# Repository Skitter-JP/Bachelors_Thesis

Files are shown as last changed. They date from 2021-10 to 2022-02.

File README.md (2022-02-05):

# Bachelors Thesis

CVUT Logo

Topic: Sensorless Field Oriented Control of a Brushless DC Motor

This thesis was written at the Czech Technical University in the department of Circuit Theory.

The Goals of this thesis were

- Select a suitable combination of a microcontroller and power electronics.
- Design the controlling electronics and a printed circuit board.
- Design and implement the controlling algorithm for the estimation of the rotor angle and the field oriented control.

In this repositary the following has been attached

- **Code:** The Code was written in Microchip Studio using C. The USB library has not been included since its not my property.
- **Schematics:** The Schematics and PCBs were designed in Altium. All footprints, symbols and 3D models were manually inserted into my own component library.
- **Boards views:** The 3D views should be opened in Adobe. Github/Chrome does not support 3D PDF models
- **3D Models:** The Motor Mounts, Magnetic Sensor Mounts and Magnet Mounts can be found here.
- **Images:** The manufactured PCB and Mounts can be viewd here.
- **Document:** The thesis document which was submitted

## ESC PCB Board Views

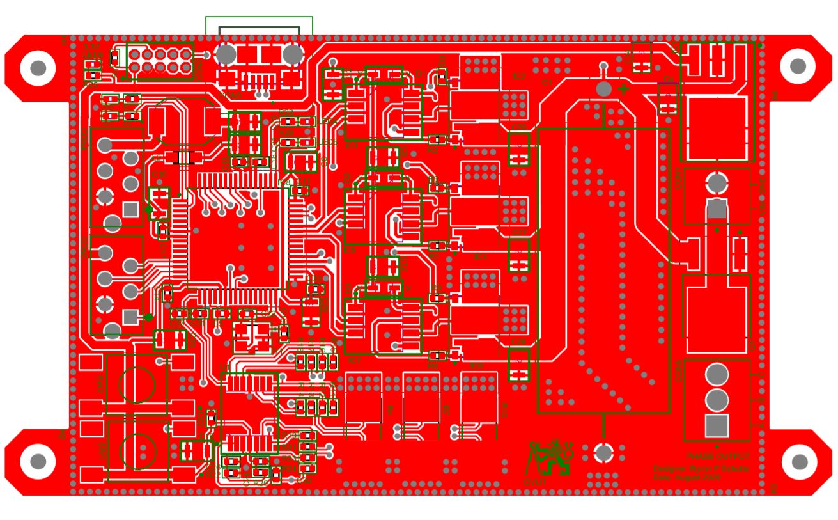
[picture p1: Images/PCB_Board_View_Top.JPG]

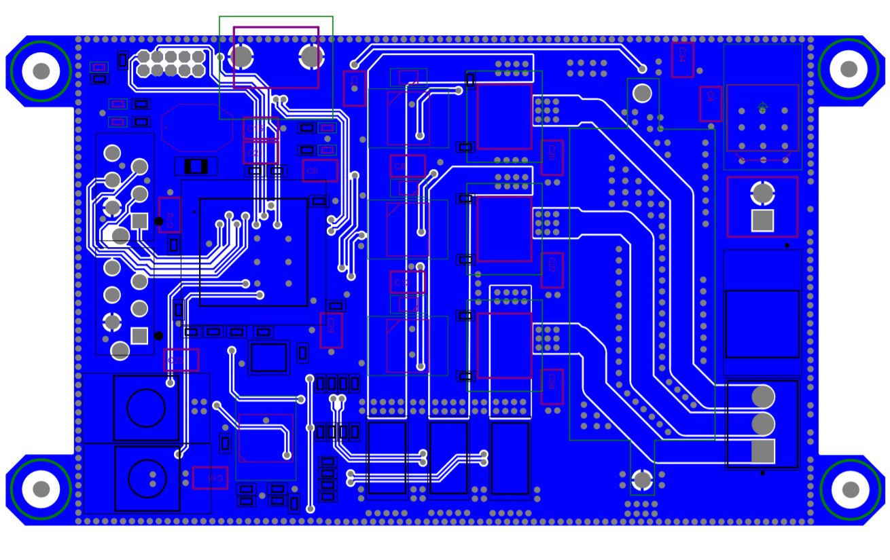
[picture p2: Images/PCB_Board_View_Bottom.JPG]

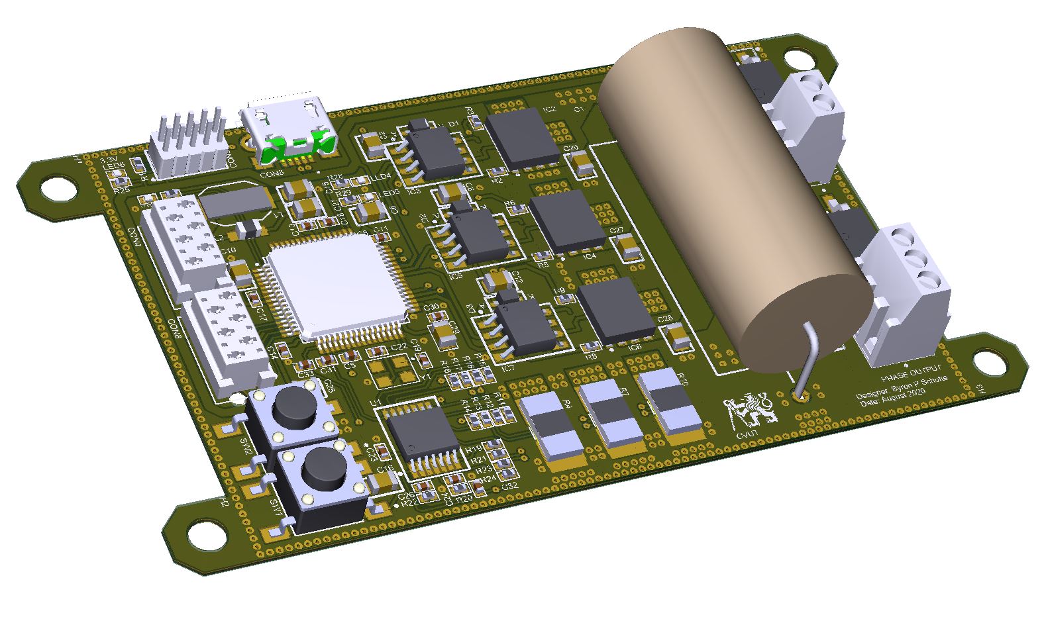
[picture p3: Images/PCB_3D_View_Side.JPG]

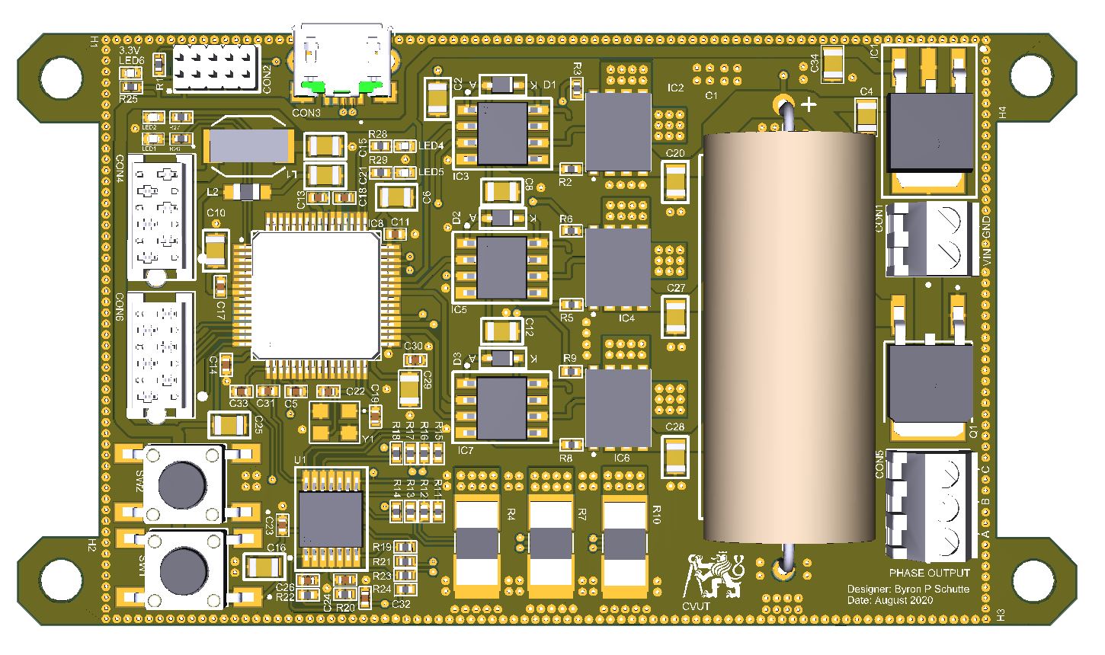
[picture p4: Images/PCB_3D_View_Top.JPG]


## Completed ESC PCB

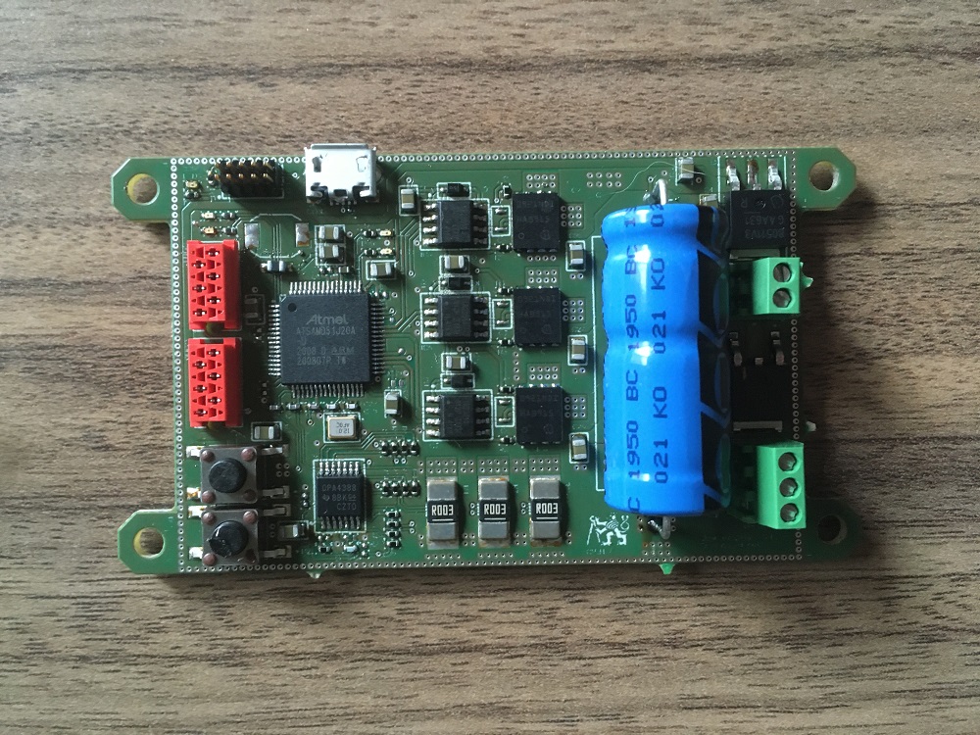
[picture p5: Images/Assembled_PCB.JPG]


## Magnetic Encoder Board Views

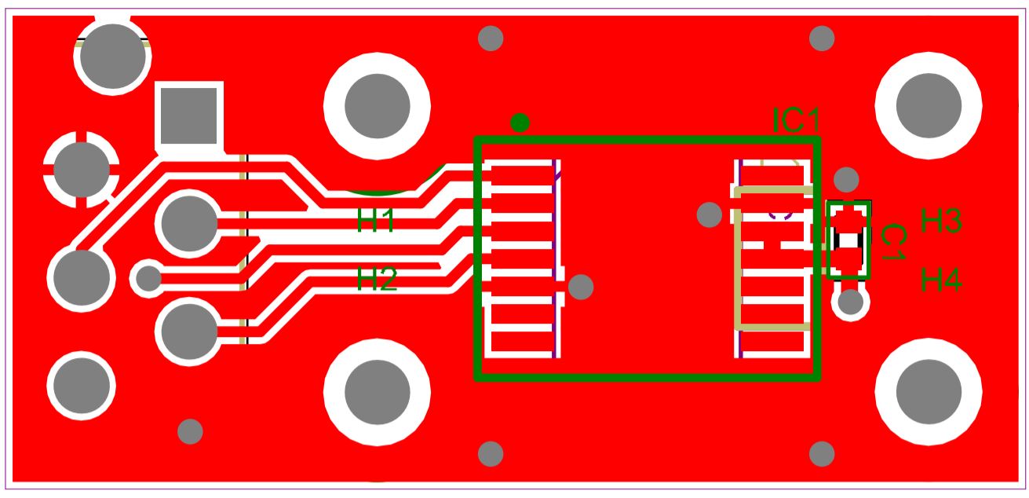
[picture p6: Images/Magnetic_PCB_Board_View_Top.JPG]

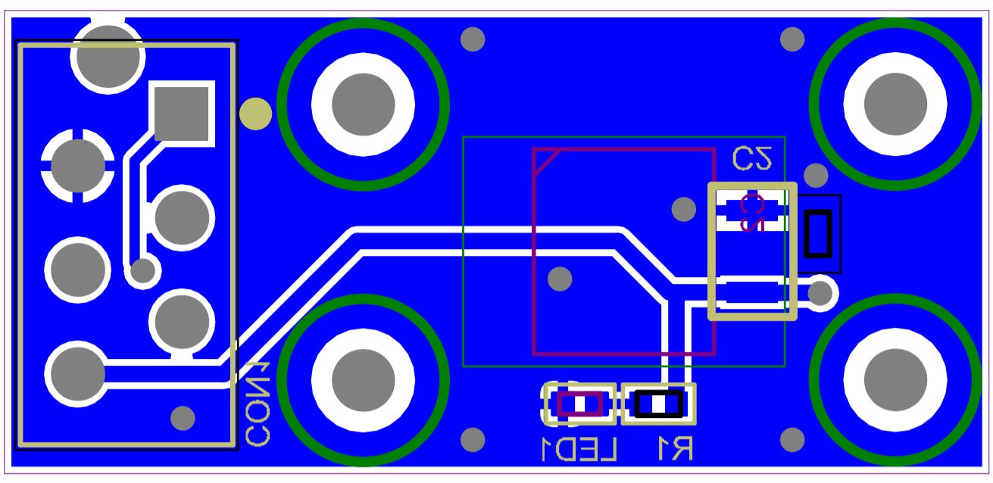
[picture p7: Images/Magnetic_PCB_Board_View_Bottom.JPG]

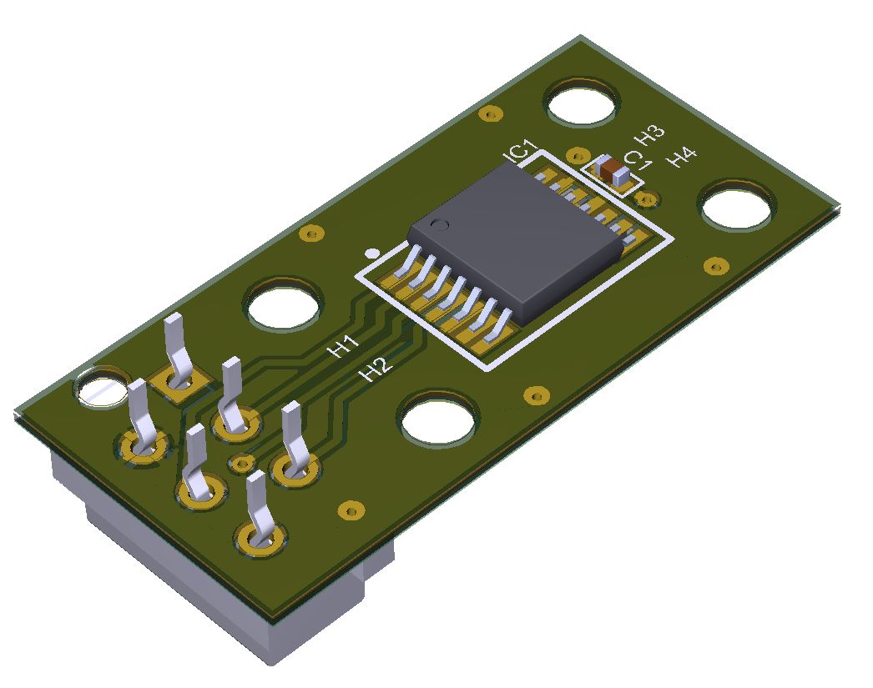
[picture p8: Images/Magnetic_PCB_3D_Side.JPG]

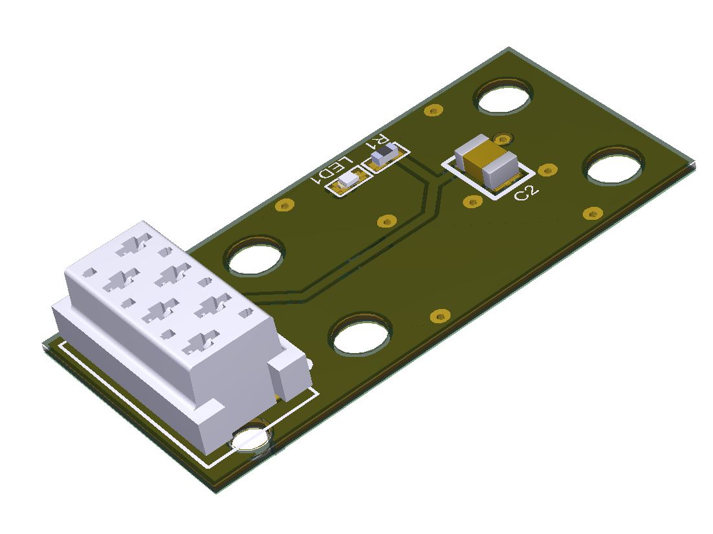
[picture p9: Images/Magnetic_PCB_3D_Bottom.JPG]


## Completed Magnetic Encoder PCB

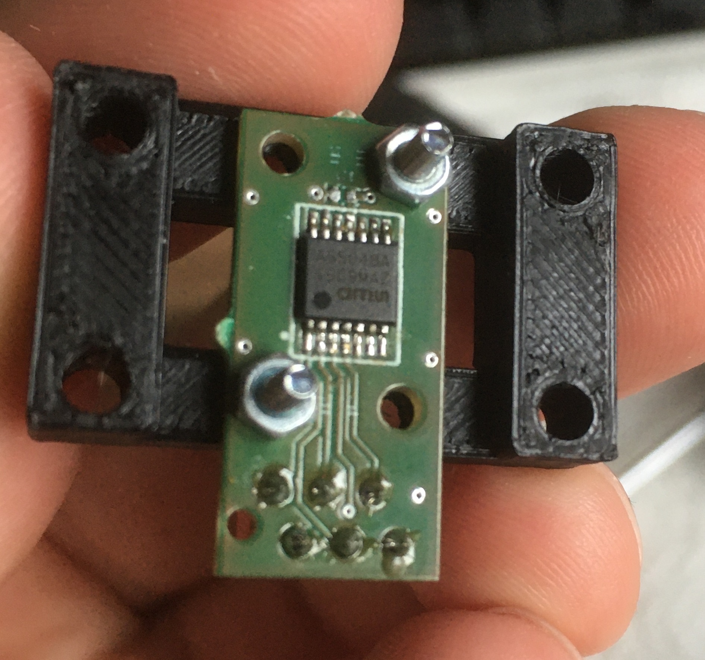
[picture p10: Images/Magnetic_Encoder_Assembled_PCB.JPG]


## Hardware Block Diagram

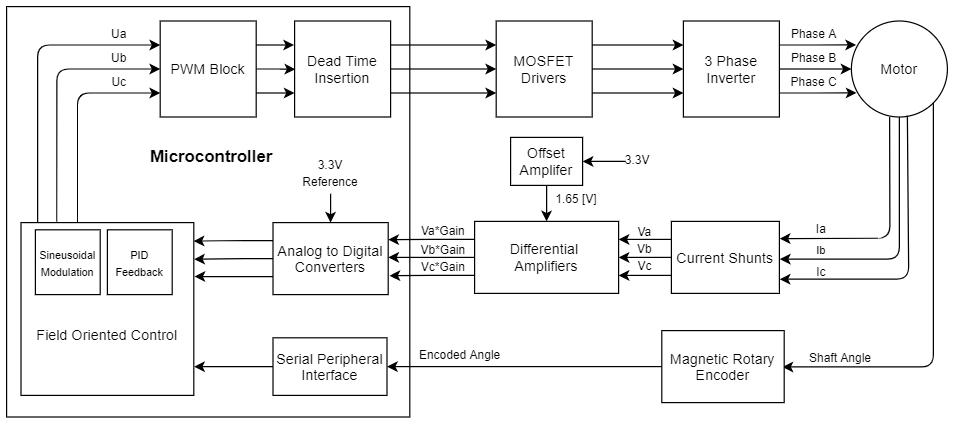
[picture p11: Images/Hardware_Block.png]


## State Observer Block Diagram

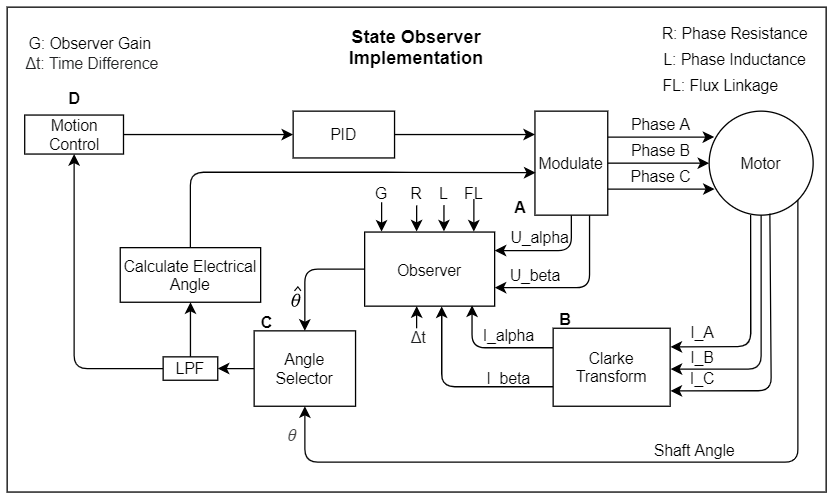
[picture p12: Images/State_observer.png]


- **A:** The modulated voltages 𝑈𝛼 and 𝑈𝛽 are passed into the Observer
- **B:** The currents generated from 𝑈𝛼 and 𝑈𝛽 are read and converted into the same reference frame (𝐼𝛼 and 𝐼𝛽) and then fed into the observer
- **C:** The angle from the observer and the encoder are passed into the angle selector, depending on the sensing mode either angle will be passed in the control loop
- **D:** The control loop handles the given angle and performs the necessary task

## Constant Velocity Mode

The following figure was captured from the ESC while operating in a constant velocity. In the figure the
velocity was set to 5 [rad/sec]. The measured velocity was fluctuating between 20 and -10 rad/sec. The
mean value was centered near 5 rad/sec.

A professor in my defense mentioned that these large fluctuations in the measured velocity were most likely caused from the BLDC motor.
A BLDC motor is designed for trapezoidal wave forms, if a BLAC motor would of been used these large fluctuations in the measured velocity would of not been apparent.

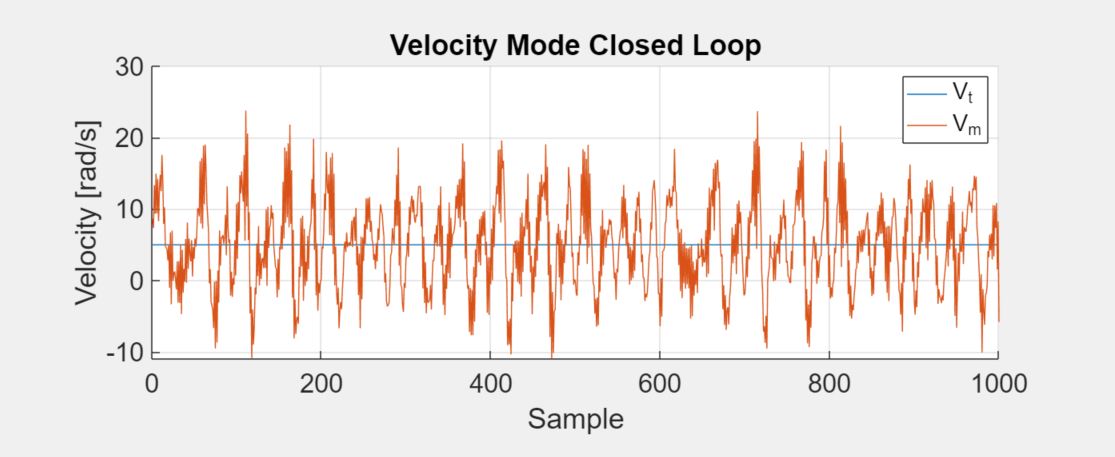
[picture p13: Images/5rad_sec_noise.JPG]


- **Vt:** Target Velocity
- **Vm:** Measured Velocity

## Current Sensing Results

The following figures were captured from the ESC while operating in a constant velocity mode at 5
rad/sec. In the first figure the motor was running with no mechanical load, the wave form appears noisy, but a sinusoidal signal is visible.
In the second figure a mechanical load was placed on the motor, this increased the consumed current. The wave form is clear with minimal noise.

Current capture **with no** mechancal load on the motor

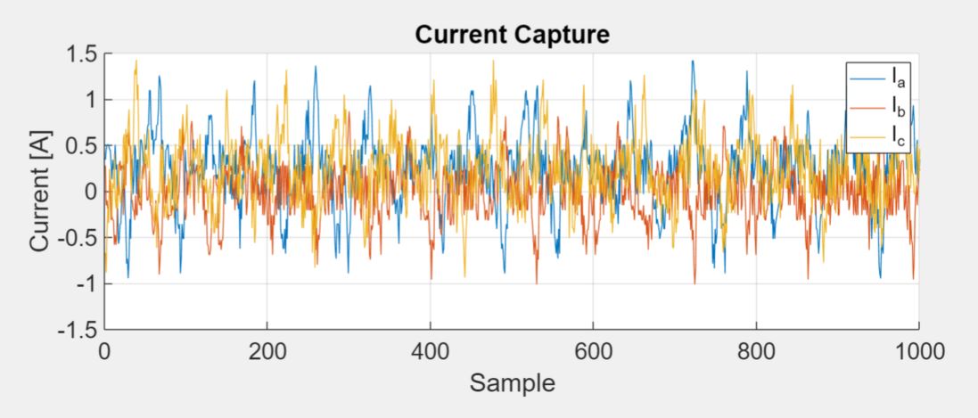
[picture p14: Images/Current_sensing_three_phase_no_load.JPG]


Current capture **with** a mechancal load on the motor

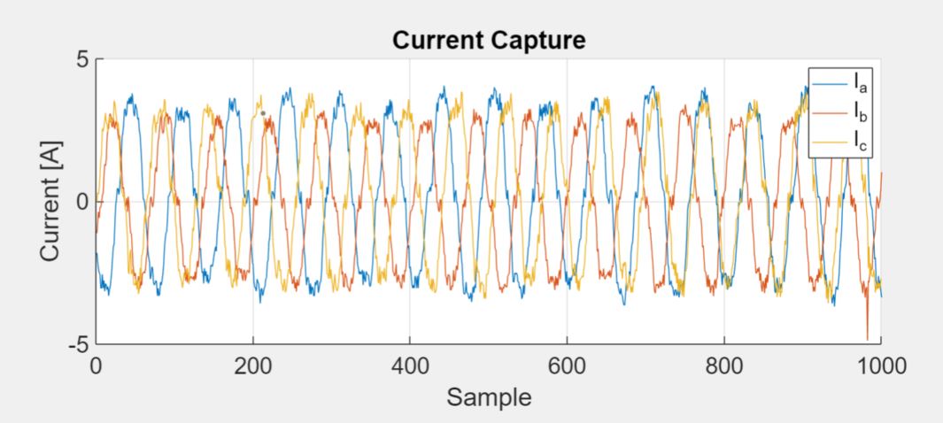
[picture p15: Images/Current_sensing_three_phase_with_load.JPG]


## Maintain Set Angle Results

The following figures demonstrate the angle closed loop functionality. In the figure below the set angle is 5 rad.
The motor shaft was mechanically displaced in both directions, the shaft returned its set point with slight over and undershoots.

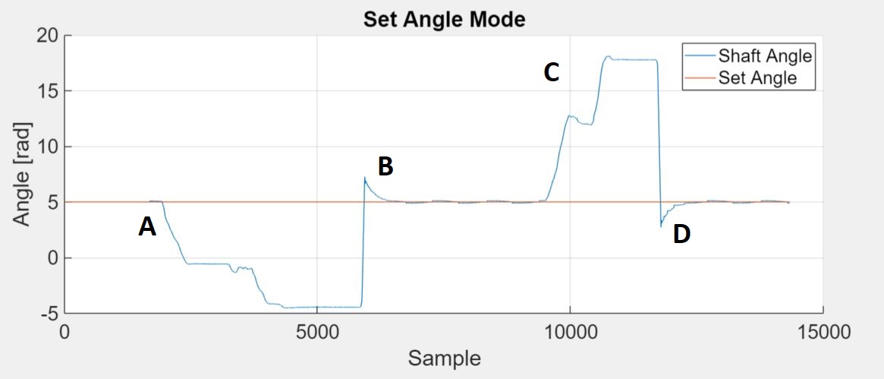
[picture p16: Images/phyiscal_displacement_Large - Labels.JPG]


- **A:** The shaft is displaced 5 rad in a negative direction
- **B:** The shaft is released, an overshoot occurs
- **C:** The shaft is displaced 15 rad in the positive direction
- **D:** The shaft is released, an undershoot occurs

## Angle Estimation Results

A state observer was implemented to estimate the angle of the motor shaft using
voltages/currents in the rotating reference frame. Estimating the shaft of the angle was possible but
was not stable. The state observer would saturate due to noise in the current measurements, therefor
to keep the estimated angle stable a load needed to be applied to the motor to push the currents out
of the noise floor.

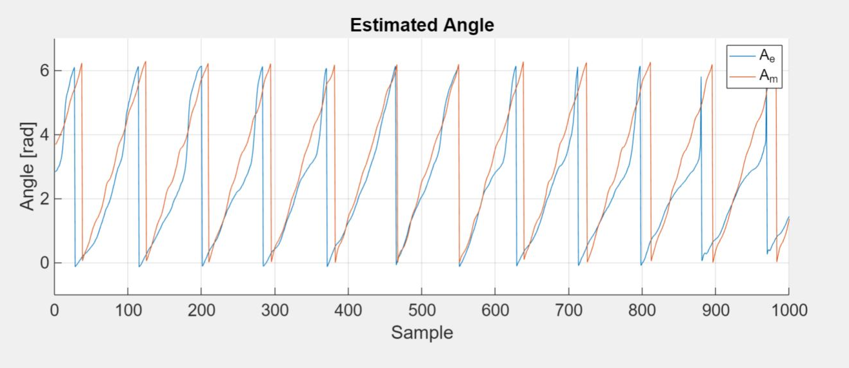
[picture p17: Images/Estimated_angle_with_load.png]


- **Ae:** Estimated Angle
- **Am:** Measured Angle 

## 3D Printed Mounts

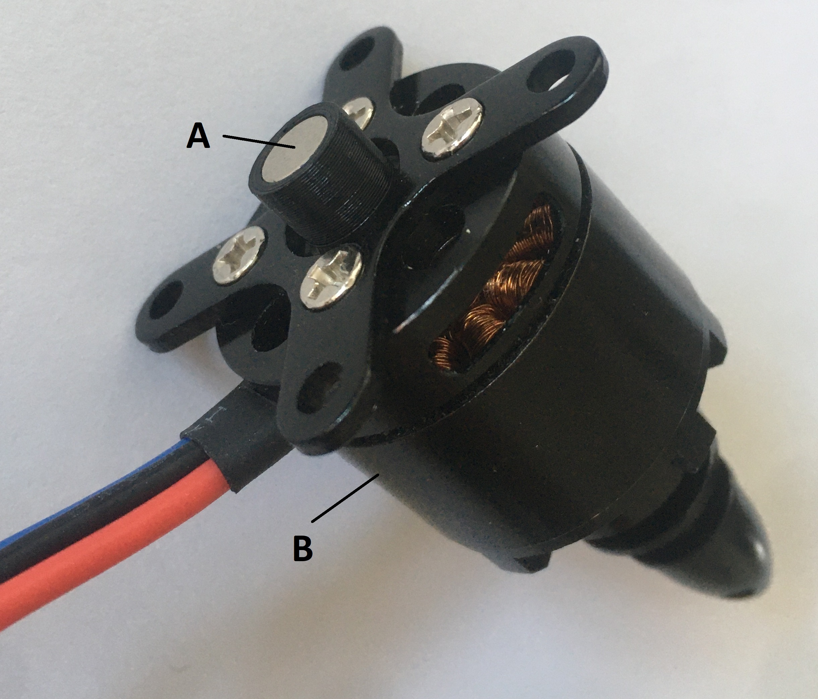
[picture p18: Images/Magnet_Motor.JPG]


- **A:** A small mount for a diametrically magnetized magnet which was mounted to the rotor.
- **B:** A BLDC Motor

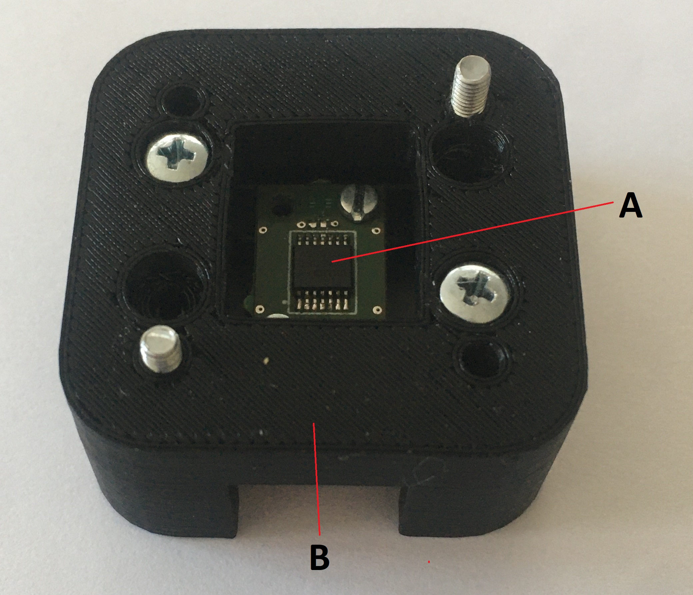
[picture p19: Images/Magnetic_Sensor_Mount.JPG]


- **A:** The magnetic encoder which was mounted just below the rotor.
- **B:** A 3D printed Motor/Magnetic encoder Mount

## Notes
1. I wanted to split the code up into seperate libraries but this obvisouly did not happen, so please excuse the mess.
2. My supervisor encouraged me to tightly layout the PCB and use small footprints. The smallest being 0402 packages, this was also a challange to solder but worth the effort.
3. The graphs and data seen in the document were created in MATLAB
4. The motor and magnetic mount were created in SketchUp 3D

Lastly, credit must be given to the [ArduinoFOC](https://github.com/simplefoc/Arduino-FOC) project. I spent weeks reading their code and porting ideas over to my project.

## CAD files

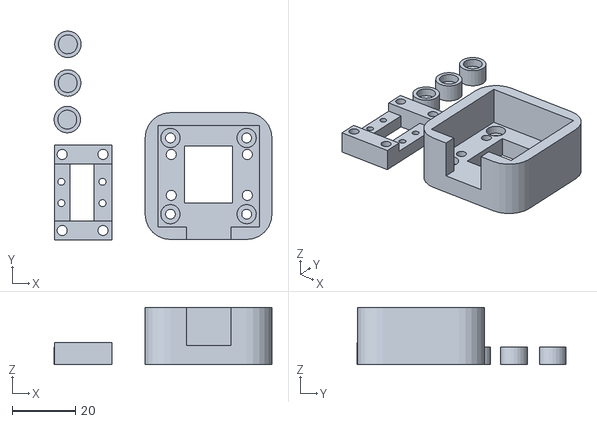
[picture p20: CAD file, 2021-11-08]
3D Models/Prints_fixed.stl
68.8 x 65.9 x 18.0

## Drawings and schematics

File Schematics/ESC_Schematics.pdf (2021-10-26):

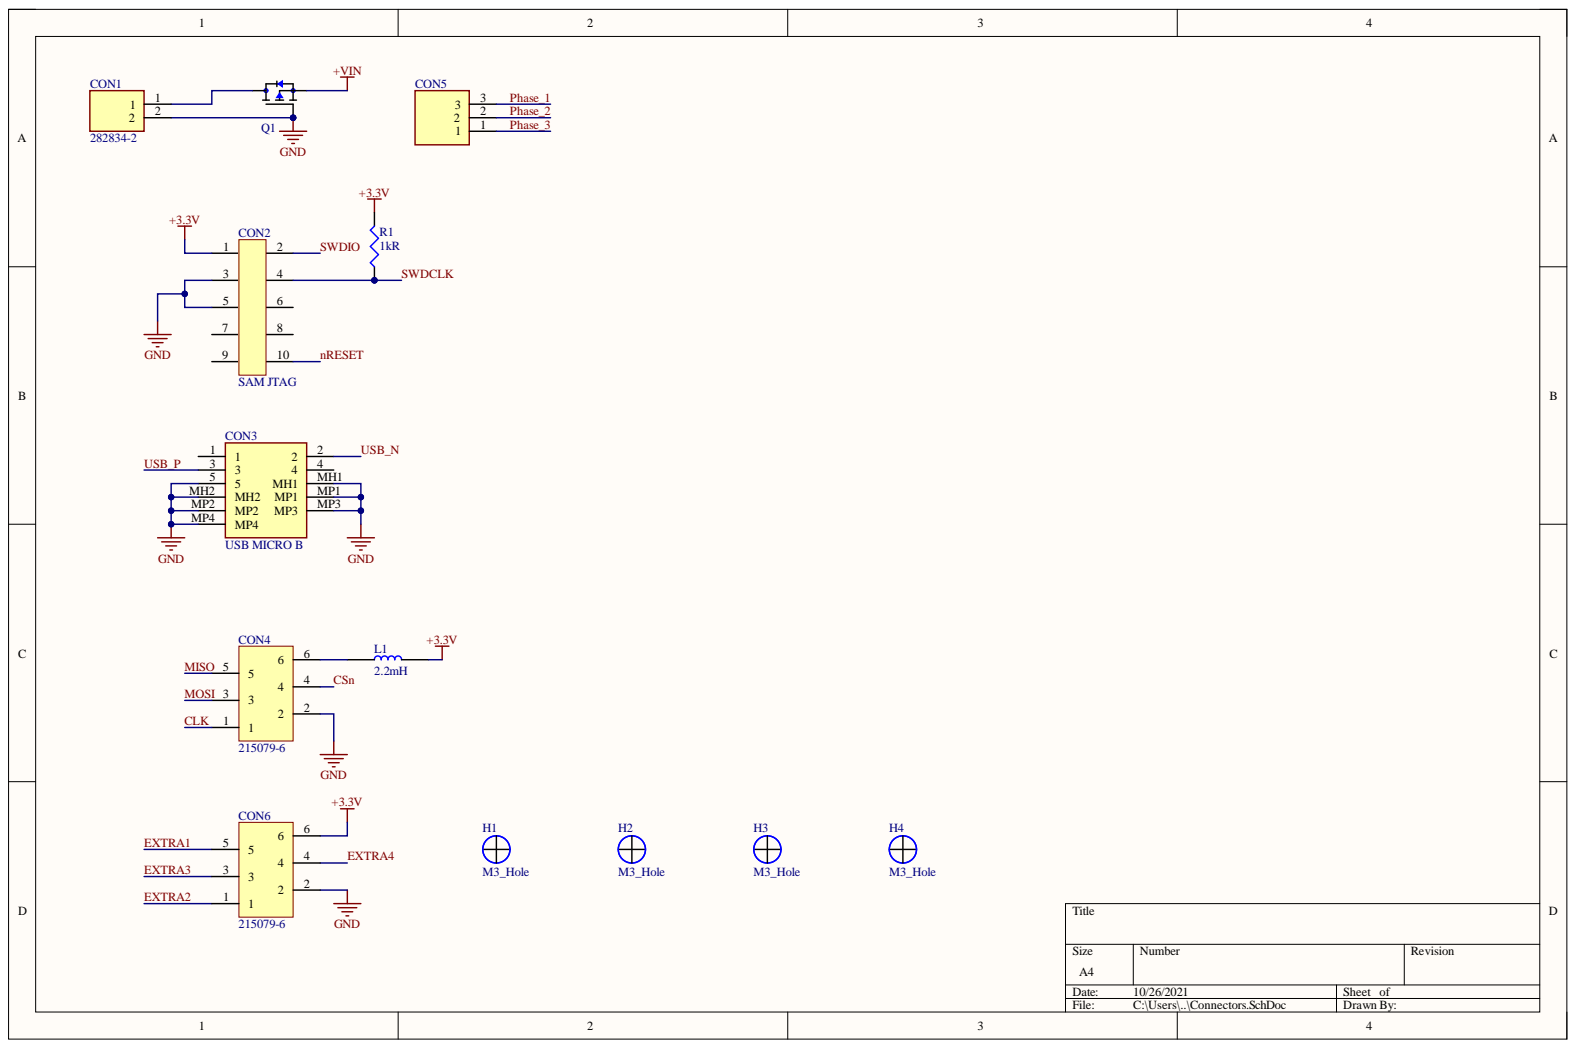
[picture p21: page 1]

Size A4 | Number | Revision

Date: 10/26/2021 | Sheet of
File: C:\Users\..\Connectors.SchDoc | Drawn By:

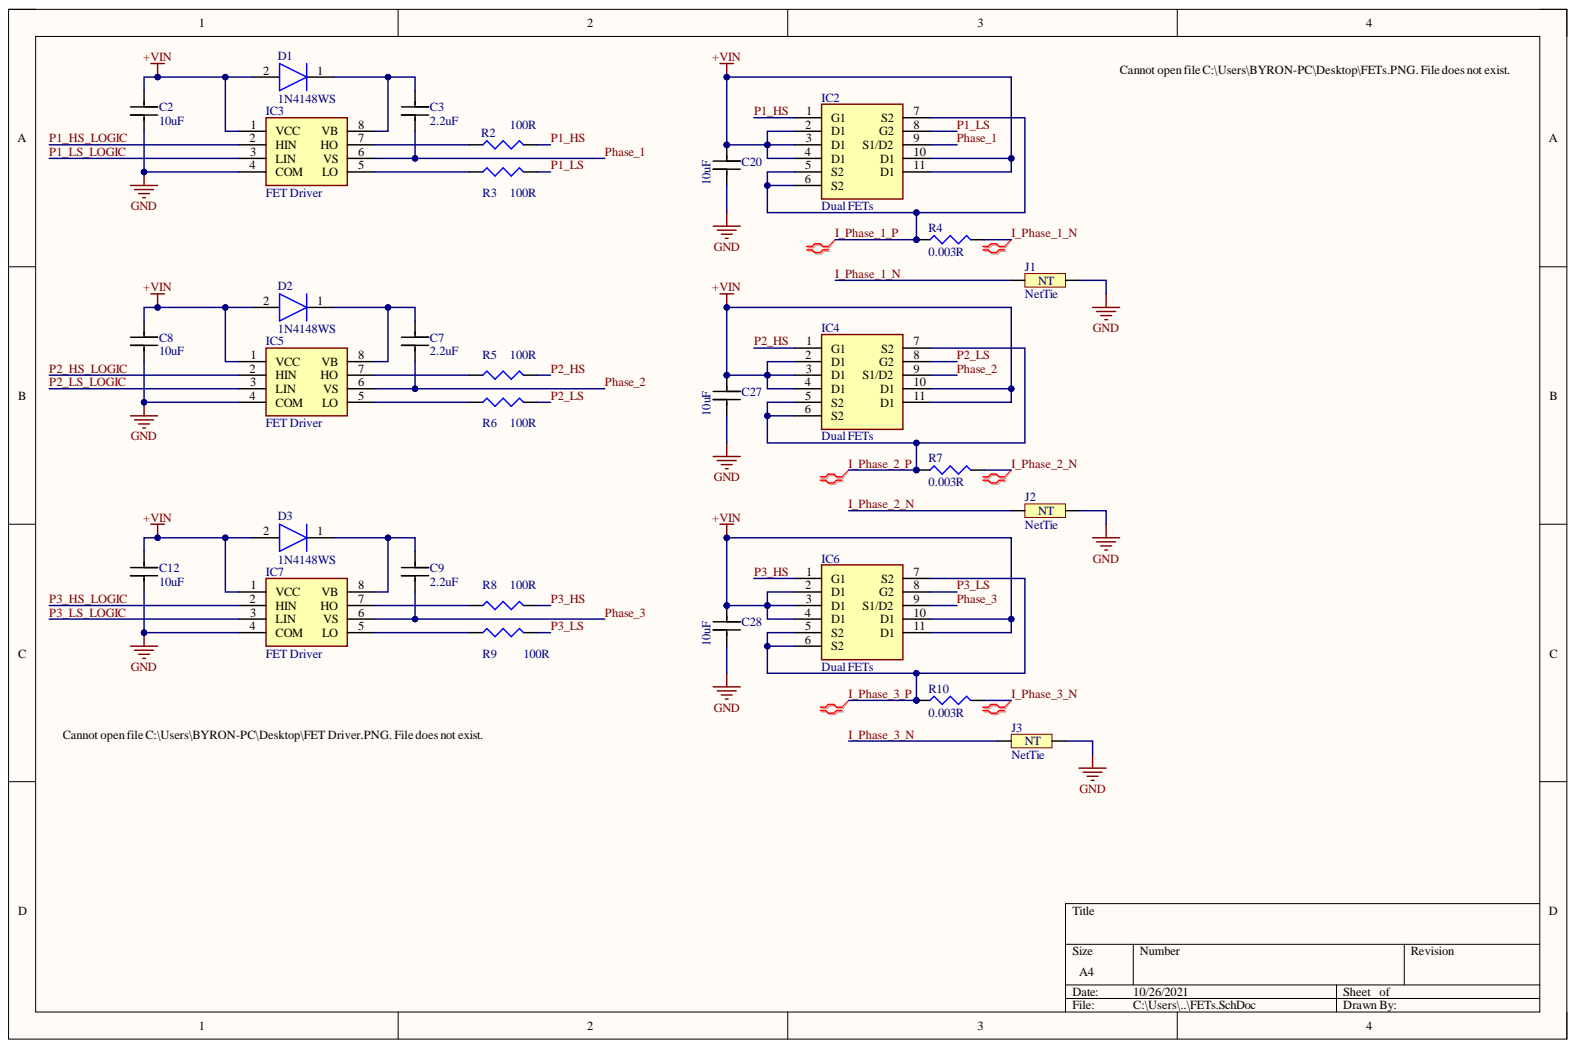
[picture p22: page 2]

Siz e A4 | Numb e r | R evisio n

Da te : 10/26/20 2 1 | She et of
File : C:\Use rs\. .\FETs. S c hD o c | Dr awn B y :

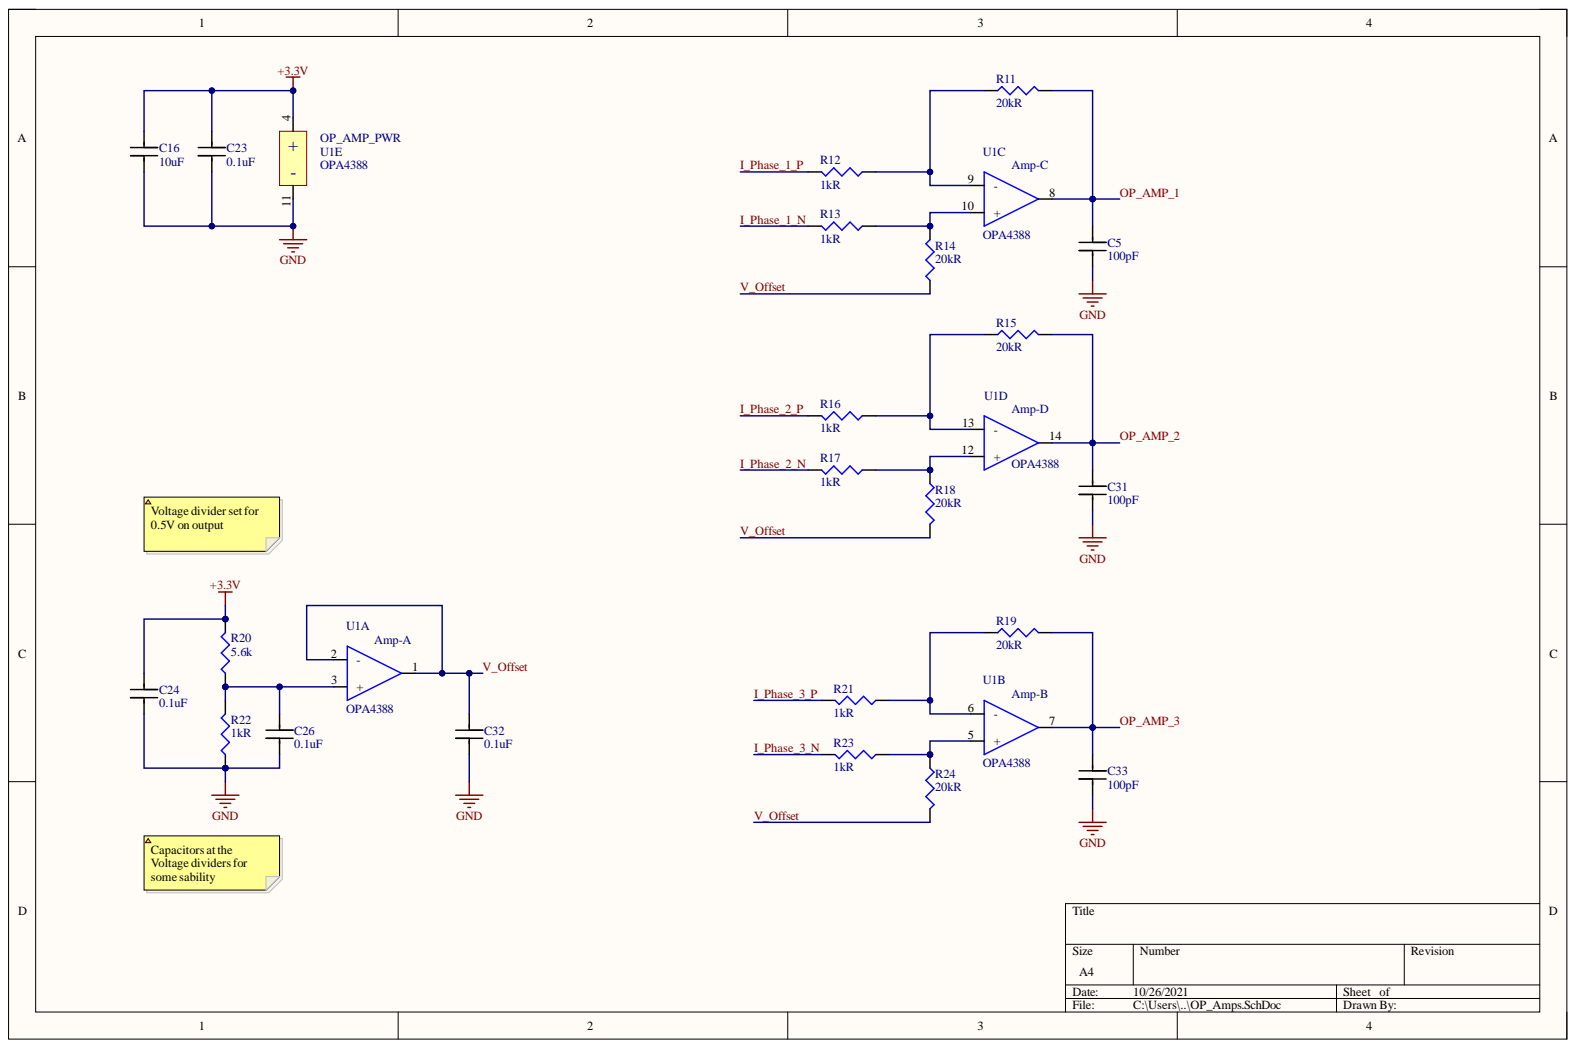
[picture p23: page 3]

some sability Voltage divide
0.5V on output

Siz e A4 | Numb e r | R evisio n

Da te : 10/26/20 2 1 | She et of
File : C:\Use rs\. .\OP_Amp s . S c hD o c | Dr awn B y :

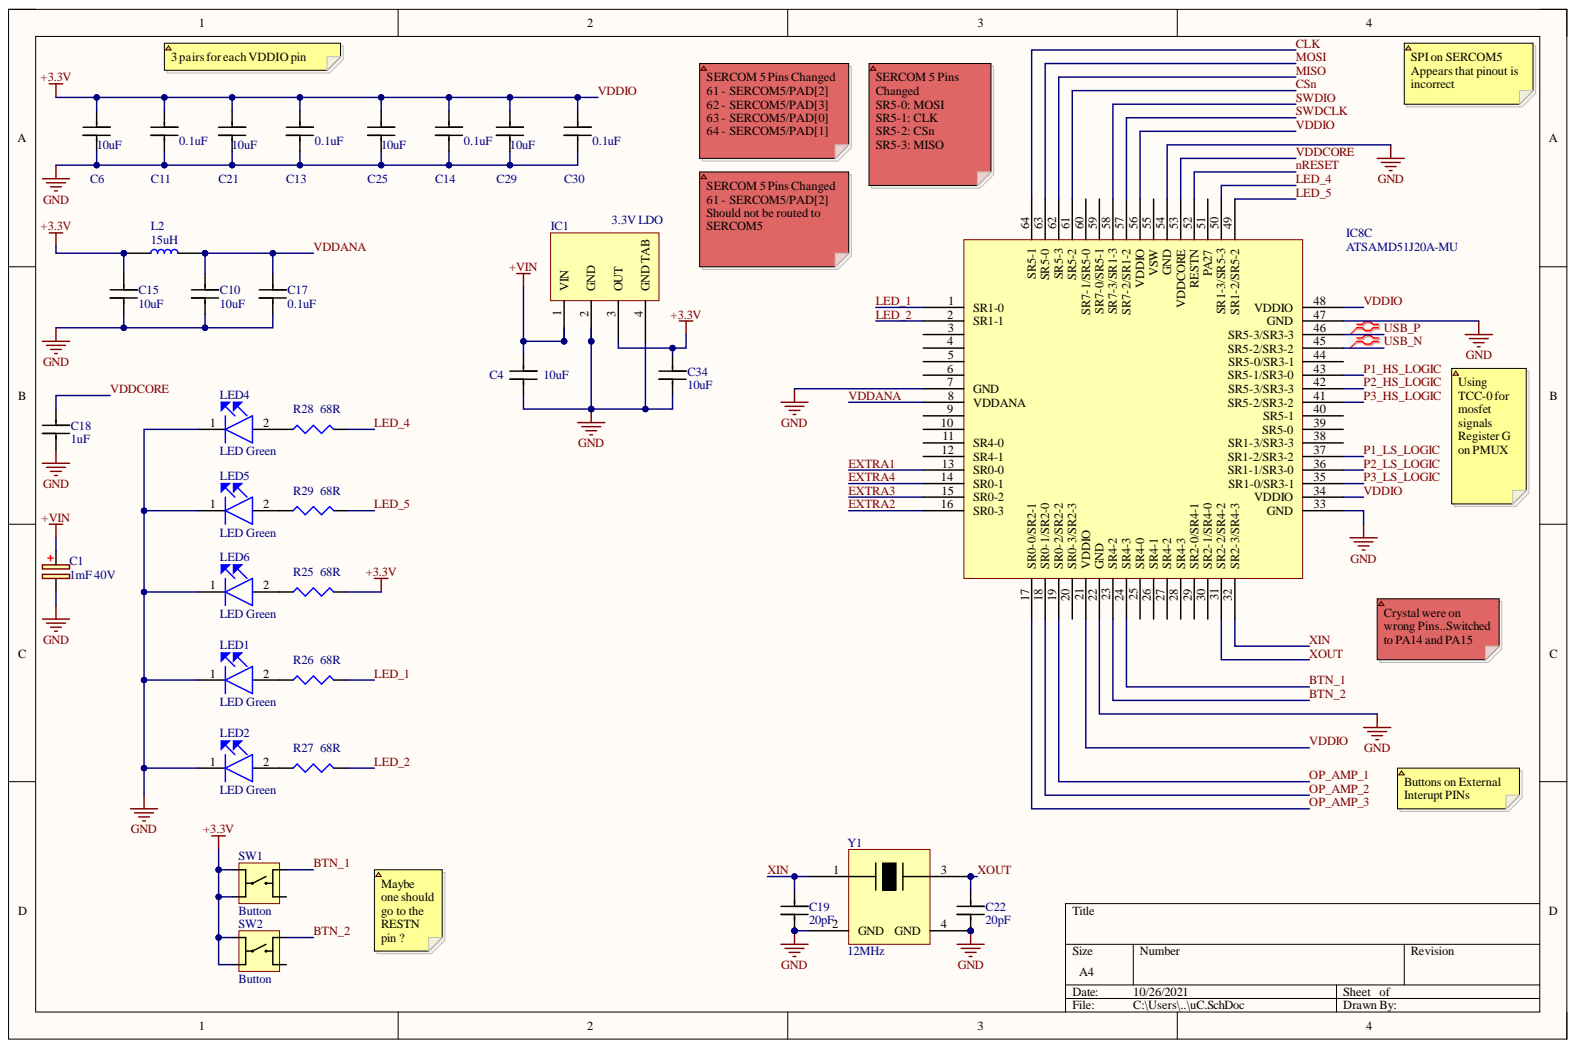
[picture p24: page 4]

CLK

VDDC O RE nRES ET LED _4 LED _5

SR1-2/SR5-2 49 SR1-3/SR5-3 50 PA27 51 RESTN 52 VDDCORE 53 GND 54 VSW 55 VDDIO 56 SR7-2/SR1-2 57 SR7-3/SR1-3 58 SR7-0/SR5-1 59 SR7-1/SR5-0 60 SR5-2 61 SR5-3 62 SR5-0 63 SR5-1 64

one should
go to the RESTN

Siz e A4 | Numb e r | R evisio n

Da te : 10/26/20 2 1 | She et of
File : C:\Use rs\. .\uC . S c hD o c | Dr awn B y :

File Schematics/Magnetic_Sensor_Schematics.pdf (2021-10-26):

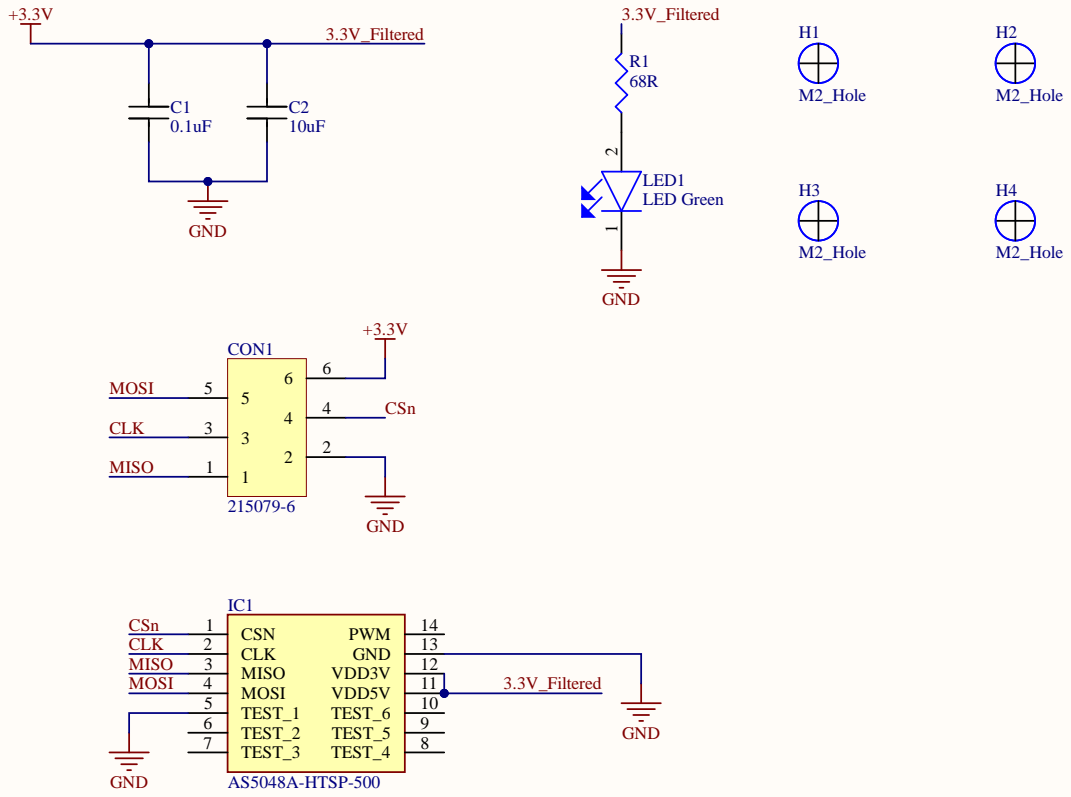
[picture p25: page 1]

MOSI 4 | 3.3V_Filtered
TEST_1 5

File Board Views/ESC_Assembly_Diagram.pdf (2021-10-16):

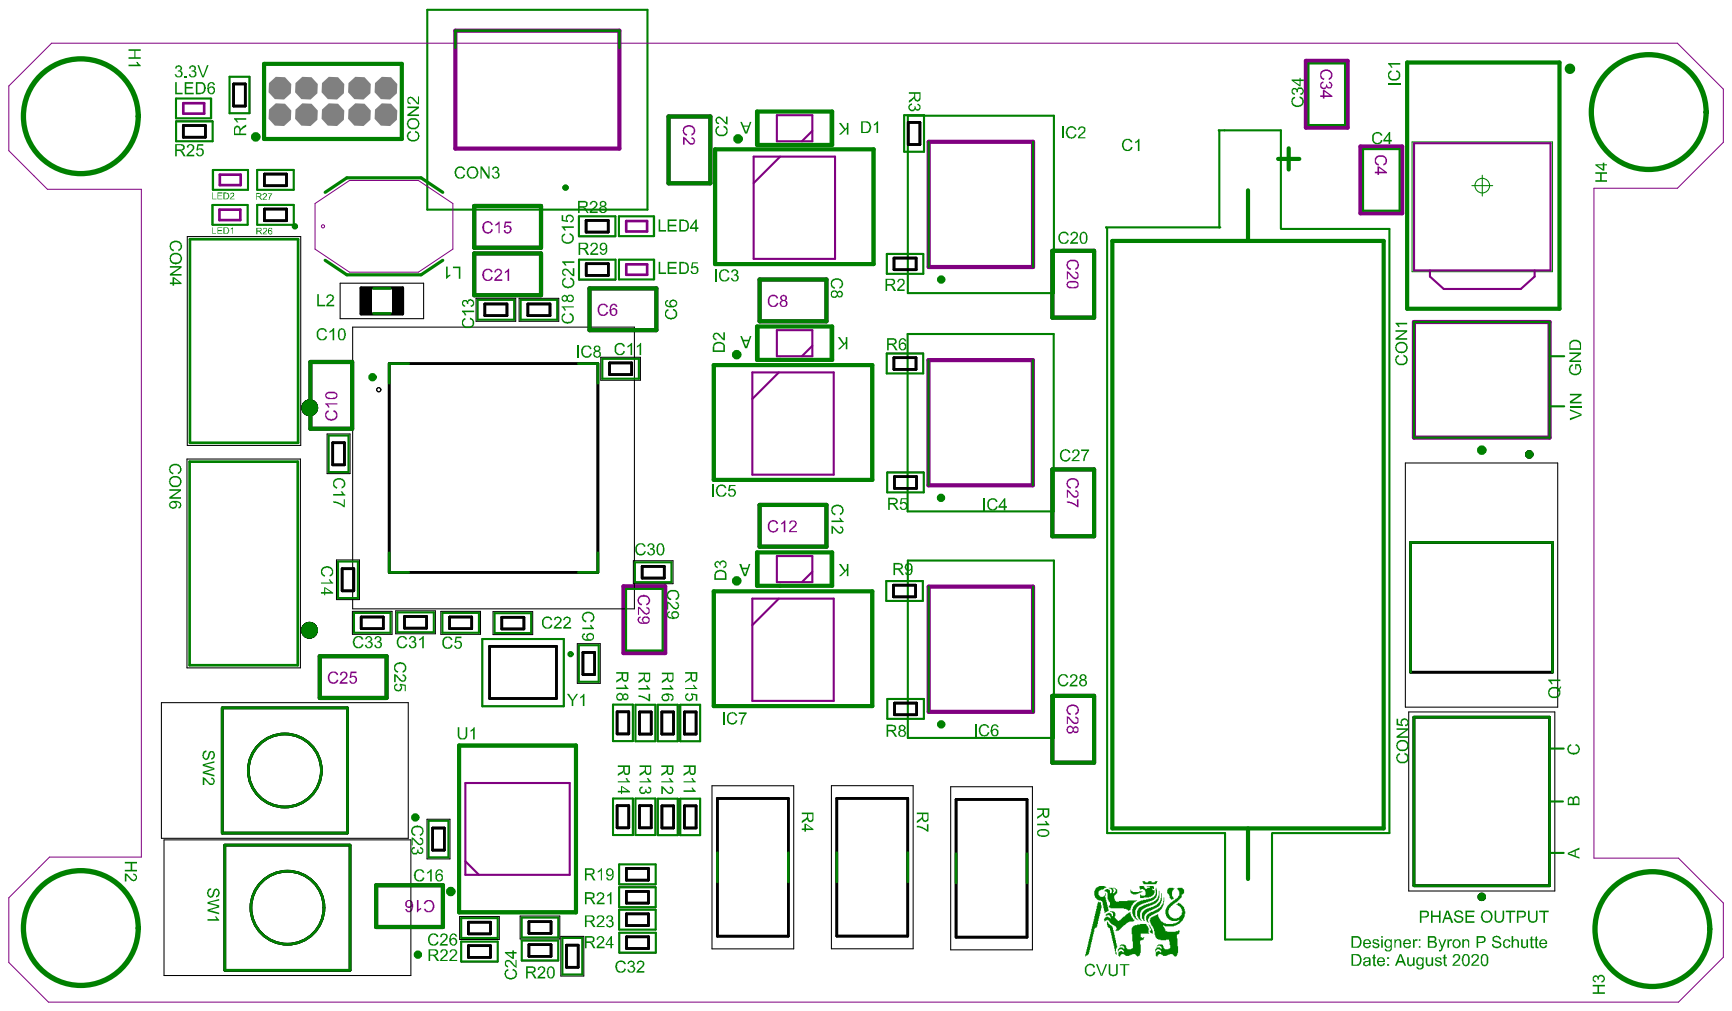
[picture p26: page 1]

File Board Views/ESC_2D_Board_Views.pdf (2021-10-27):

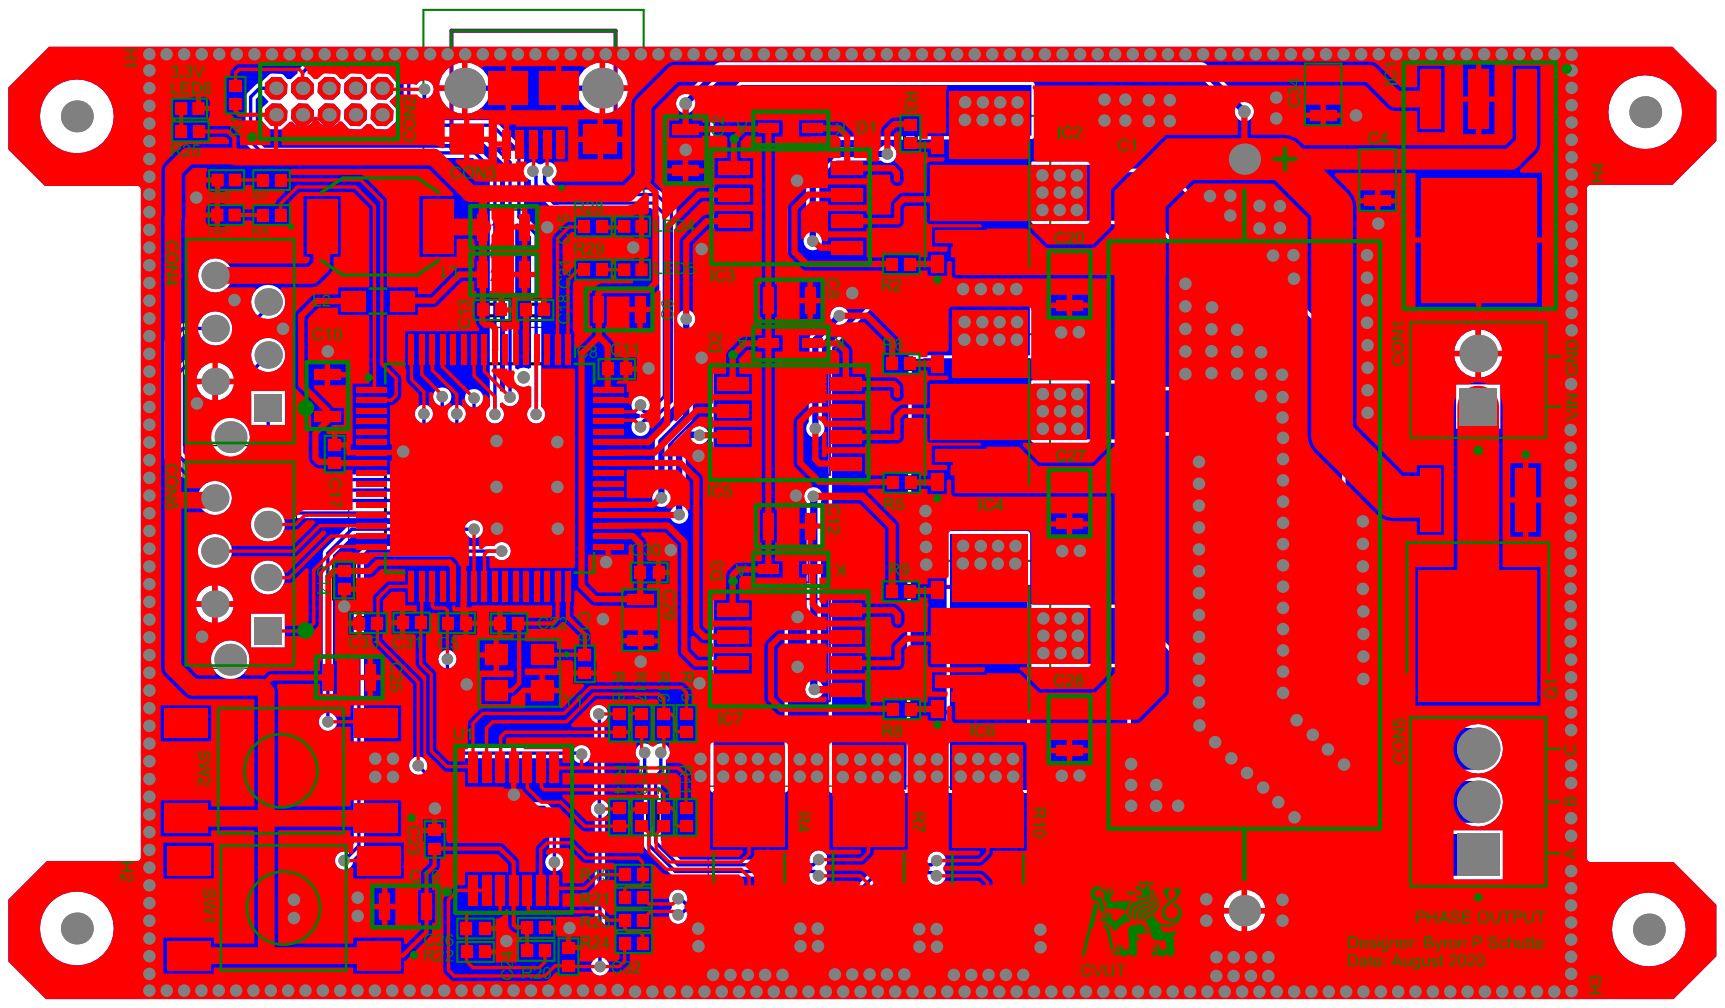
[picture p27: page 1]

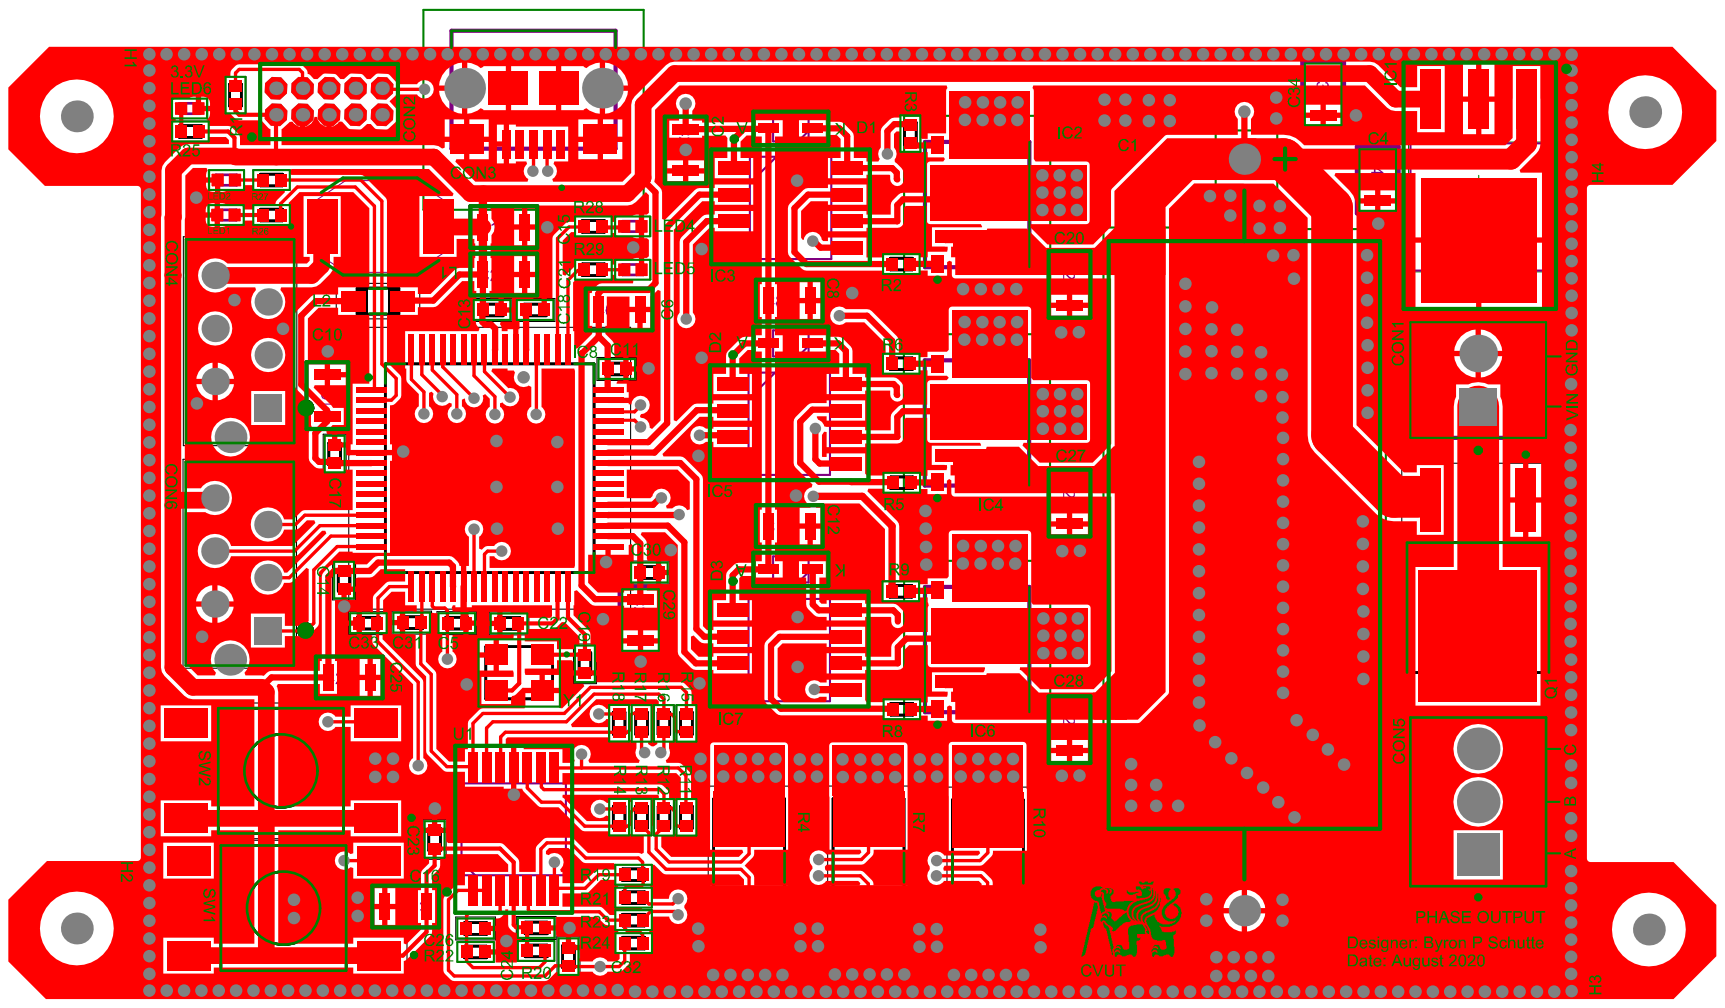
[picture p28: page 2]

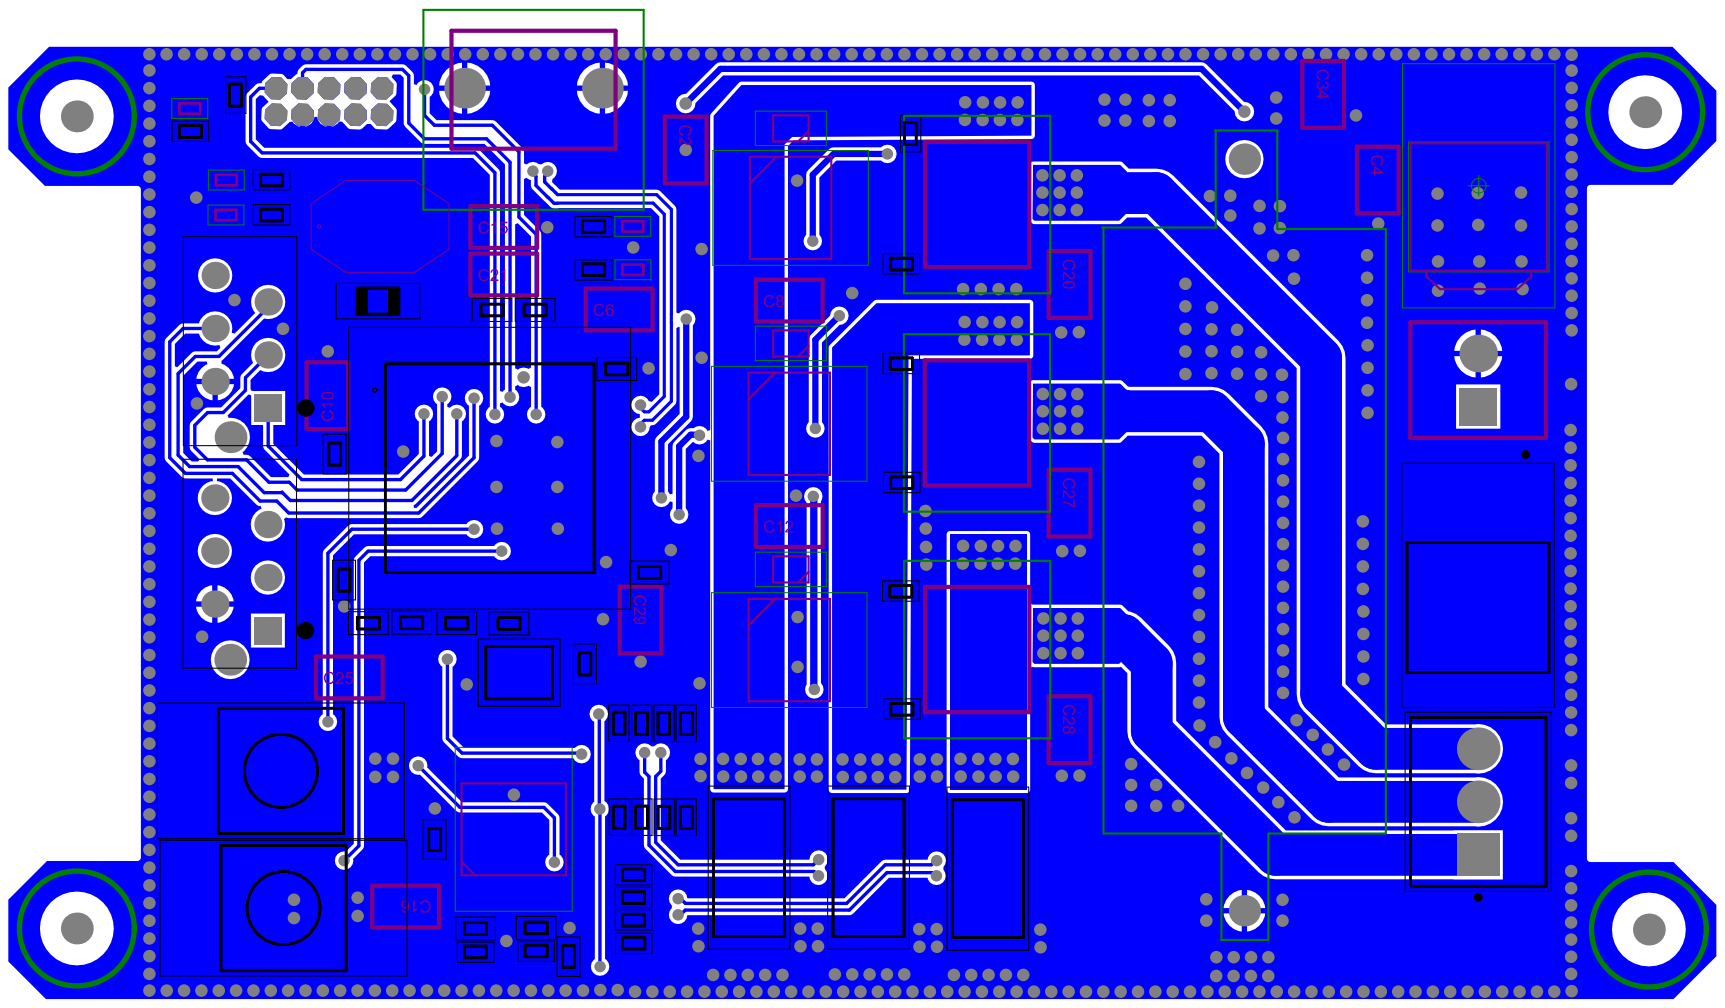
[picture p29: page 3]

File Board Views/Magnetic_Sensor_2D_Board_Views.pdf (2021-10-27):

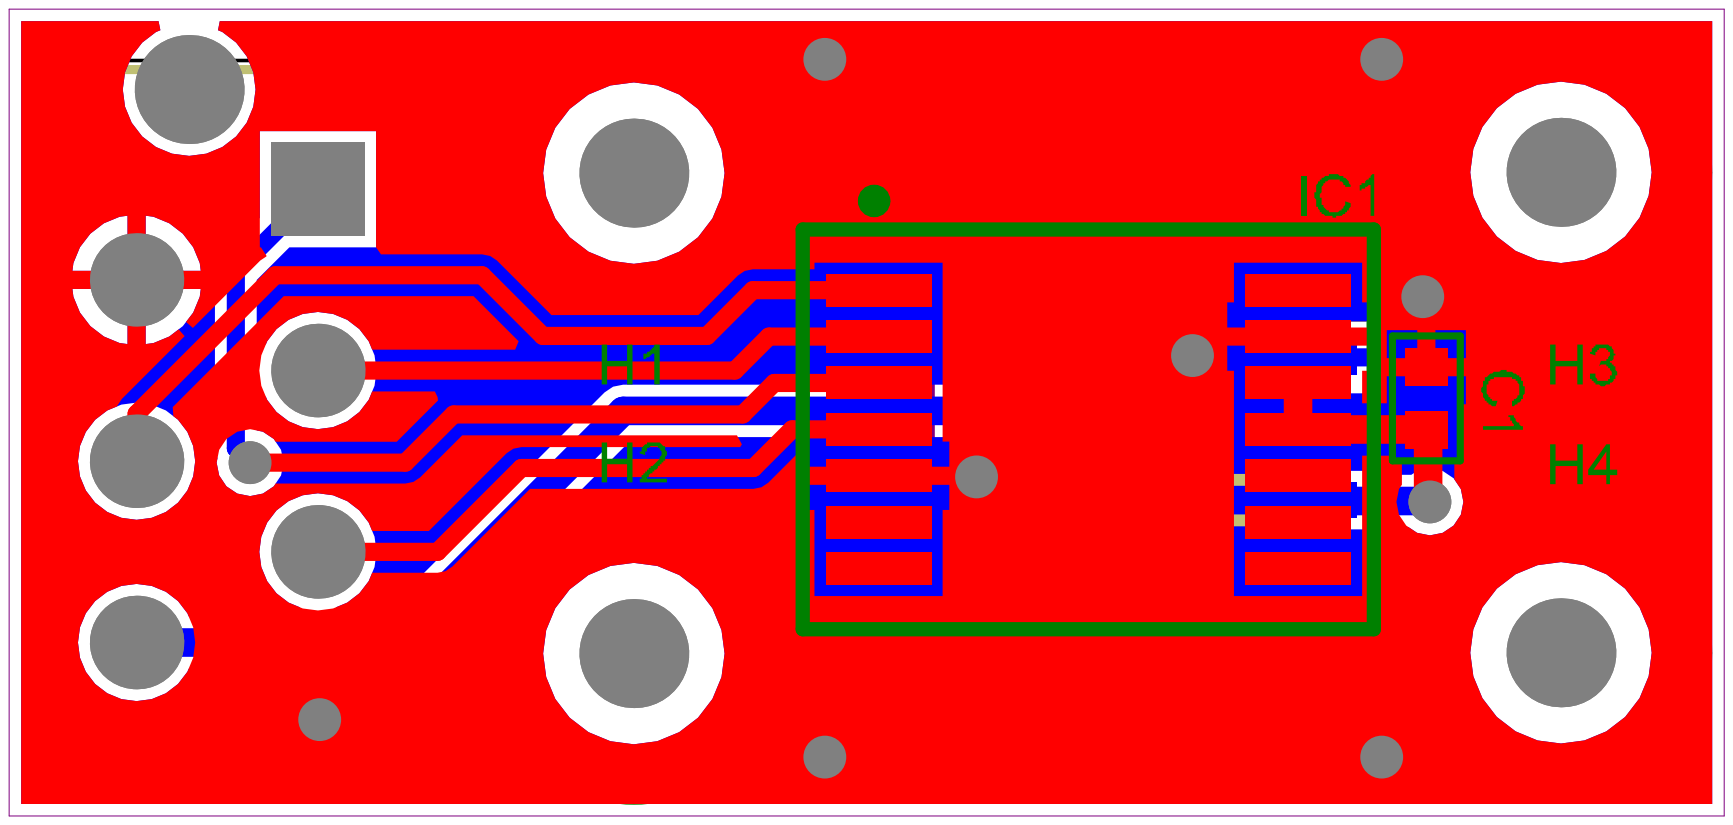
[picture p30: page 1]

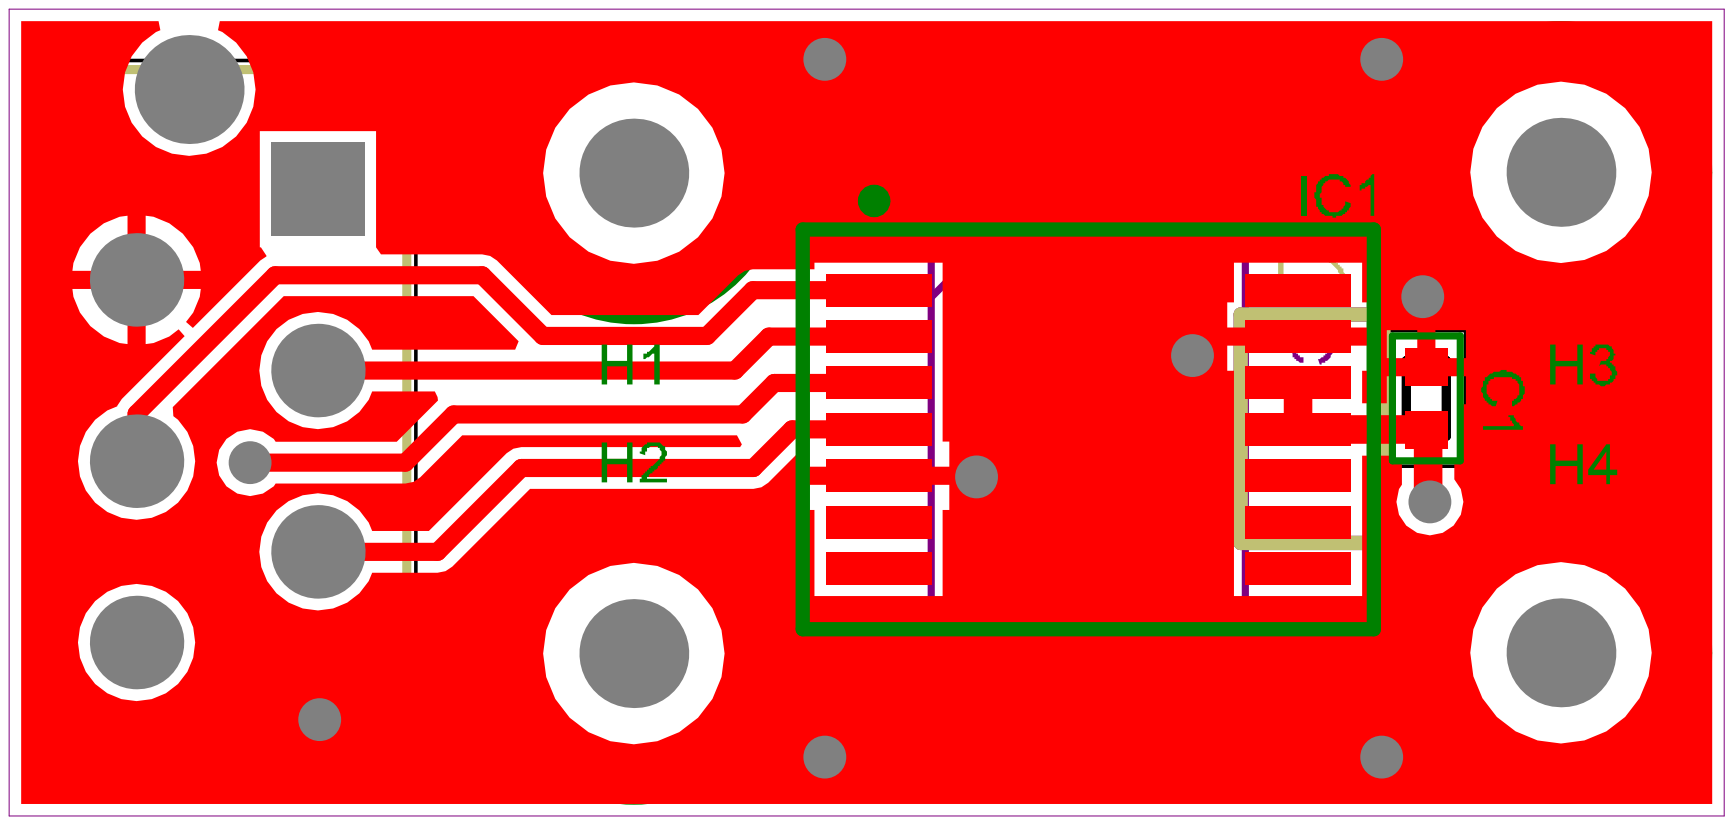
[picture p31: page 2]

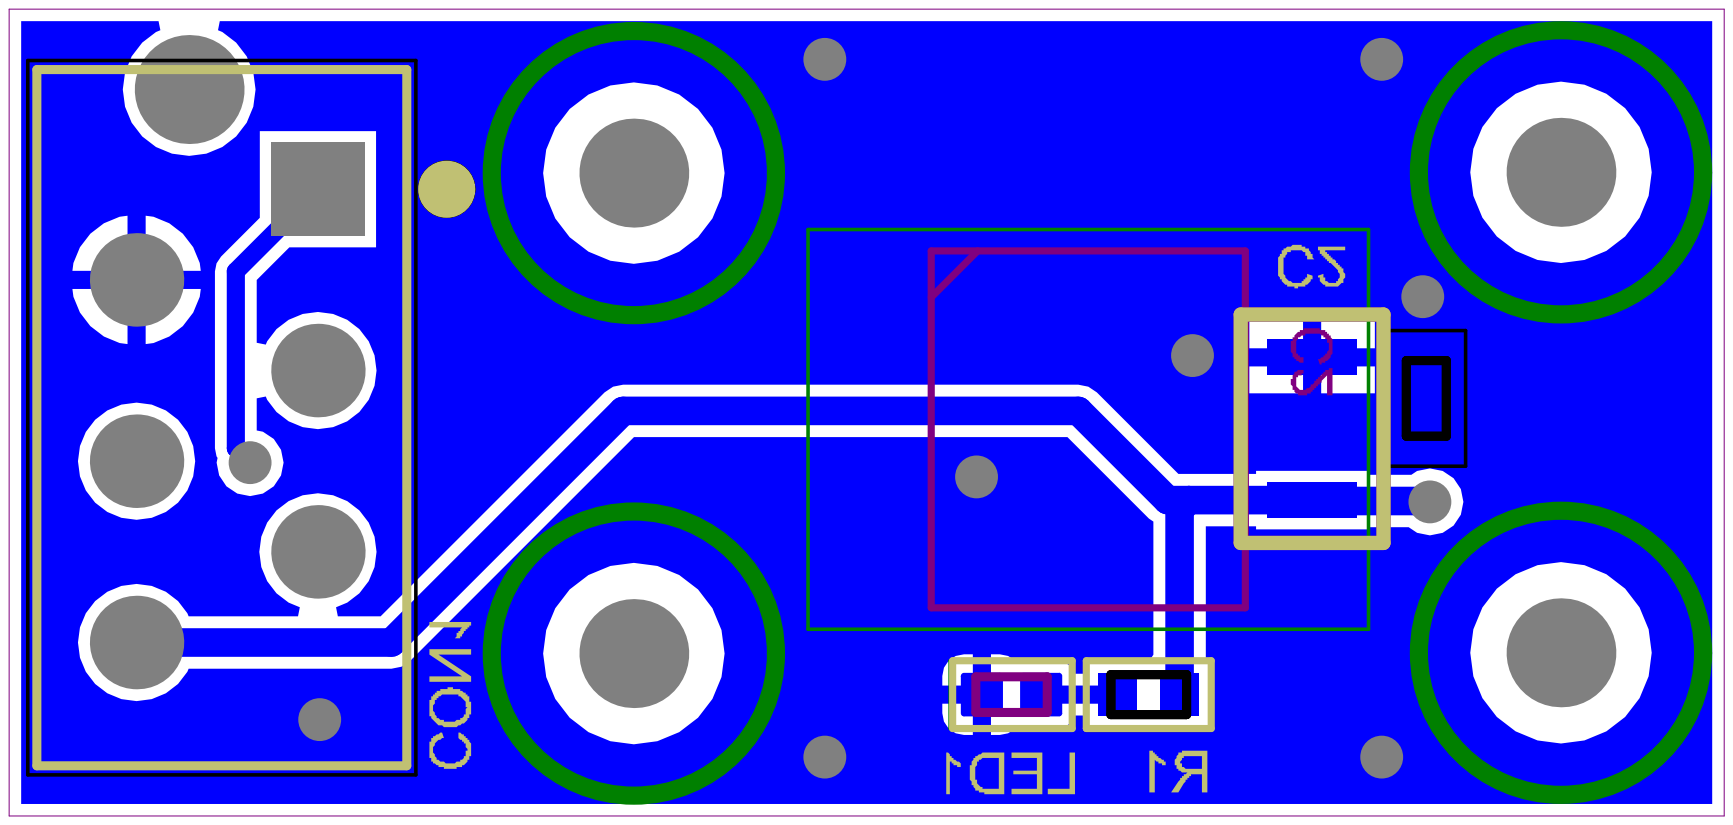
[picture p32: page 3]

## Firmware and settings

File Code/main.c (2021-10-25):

#include "sam.h"
#include "pin_macros.h"
#include "pinout.h"
#include "USB.h"
#include <string.h>
#include <math.h>
#include "tgmath.h"

typedef struct PID_struct{
	
	float P; //!< Proportional gain
	float _I; //!< Integral gain
	float D; //!< Derivative gain
	float output_ramp; //!< Maximum speed of change of the output value
	float limit; //!< Maximum output value
	float integral_prev; //!< last integral component value
	float error_prev; //!< last tracking error value
	unsigned long timestamp_prev; //!< Last execution timestamp
	float output_prev;  //!< last pid output value
	
}PID_struct;

typedef struct LPF_struct{
	
	volatile float Tf; //!< Low pass filter time constant
	volatile unsigned long timestamp_prev;  //!< Last execution timestamp
	volatile float y_prev; //!< filtered value in previous execution step
	
}LPF_struct;

typedef struct PWM_struct{

	float voltage_power_supply;
	float voltage_limit;

	float PWM_resolution;

	int modulation_type;

	volatile float dc_a;
	volatile float dc_b;
	volatile float dc_c;

}PWM_struct;

typedef struct OBSERVER_struct{

	unsigned long timestamp_prev; 
	unsigned long timestamp_now; 

	float flux_linkage;
	float observer_gain;	
	
	float x2;
	float x1;
	
	float flux_vector_alpha;
	float flux_vector_beta;
	
	volatile float xa;
	
	volatile float xb;

}OBSERVER_struct;

typedef struct MOTOR_struct{
	
	_Bool sensorless;

	int pole_pairs;
	int motor_state;

	float phase_resistance;
	float inductance;
	float flux_linkage;
	float observer_gain;

	float current_limit;

	float current_sp;
	
	volatile float exact_shaft_angle;
	
	volatile float shaft_angle;
	
	volatile float shaft_velocity;

	volatile float estimated_angle;
	
	volatile float measured_angle;

	volatile float electrical_angle;

	
	volatile float U_phase_A;
	volatile float U_phase_B;
	volatile float U_phase_C;
	
	volatile float U_q;
	volatile float U_d;
	
	volatile float U_q_prime;
	volatile float U_d_prime;
	
	volatile float U_alpha;
	volatile float U_beta;
	
	volatile float U_alpha_prime;
	volatile float U_beta_prime;
	
	volatile float I_phase_A;
	volatile float I_phase_B;
	volatile float I_phase_C;
	
	volatile float I_q;
	volatile float I_d;
	
	volatile float I_alpha;
	volatile float I_beta;
	
	
	
}MOTOR_struct;

typedef struct CURRENT_SENSE_struct{
	
	

	float shunt_resistor;
	float reference_voltage;
	float gain;
	float bit_rate;

	float volts_to_amps_ratio;

	float I_phase_A_offset;
	float I_phase_B_offset;
	float I_phase_C_offset;

	float I_gain_phase_A;
	float I_gain_phase_B;
	float I_gain_phase_C;

	float conversion_scalar;
	
	volatile uint32_t I_raw_phase_A;
	volatile uint32_t I_raw_phase_B;
	volatile uint32_t I_raw_phase_C;
	
	volatile float I_raw_phase_A_voltage;
	volatile float I_raw_phase_B_voltage;
	volatile float I_raw_phase_C_voltage;
	
	volatile _Bool read_currents;


}CURRENT_SENSE_struct;

enum Sensor_Direction{
	CLOCK_WISE = 1,
	COUNTER_CLOCK_WISE = -1,
	NONE
};

enum modulation{
	SINE_PWM,
	SPVM
};

enum calcuations{
	APROXIMATE,
	COMPUTE
};

enum states{
	DISABLED = 0,
	ENABLED = 1,
	UNKNOWN = 2
};

enum phases{

	PHASE_A = 1,
	PHASE_B = 2,
	PHASE_C = 3
	
};

enum bools{
	FALSE = 0,
	TRUE = 1
};

enum motions{
	ANGLE = 0,
	ANGLE_OPENLOOP = 1,
	VELOCITY = 2,
	VELOCITY_OPENLOOP = 3,
	TORQUE = 4
};

#define _NOP() do { __asm__ __volatile__ ("nop"); } while (0)

#define bitRead(value, bit) (((value) >> (bit)) & 0x01)
#define bitSet(value, bit) ((value) |= (1UL << (bit)))
#define bitClear(value, bit) ((value) &= ~(1UL << (bit)))
#define bitWrite(value, bit, bitvalue) (bitvalue ? bitSet(value, bit) : bitClear(value, bit))
#define bit(b) (1UL << (b))


//#define CPU_CLK (120000000ul) 
#define F_CPU	(120000000ul) //120 MHz

#define SERCOM_SPI_FREQ_REF 48000000 // 48MHz

//NaN and Infinity checks
#define UTILS_IS_INF(x)		((x) == (1.0 / 0.0) || (x) == (-1.0 / 0.0))
#define UTILS_IS_NAN(x)		((x) != (x))
#define UTILS_NAN_ZERO(x)	(x = UTILS_IS_NAN(x) ? 0.0 : x)

// Value for PCHCTRLm Mapping
#define GCLK_TCC0 25
#define GCLK_TCC2 29
#define GCLK_TC0 9

#define PORT_MUX_B 1
#define PORT_MUX_D 3
#define PORT_MUX_F 5
#define PORT_MUX_G 6
#define PORT_MUX_H 7

//For Clock Setup
#define GENERIC_CLOCK_GENERATOR_MAIN      (0u)
#define GENERIC_CLOCK_GENERATOR_XOSC32K   (3u)
#define GENERIC_CLOCK_GENERATOR_48M		  (1u)
#define GENERIC_CLOCK_GENERATOR_48M_SYNC	GCLK_SYNCBUSY_GENCTRL1
#define GENERIC_CLOCK_GENERATOR_100M	  (2u)
#define GENERIC_CLOCK_GENERATOR_100M_SYNC	GCLK_SYNCBUSY_GENCTRL2
#define GENERIC_CLOCK_GENERATOR_12M       (4u)
#define GENERIC_CLOCK_GENERATOR_12M_SYNC   GCLK_SYNCBUSY_GENCTRL4
#define MAIN_CLOCK_SOURCE				  GCLK_GENCTRL_SRC_DPLL0
#define GENERIC_CLOCK_GENERATOR_1M		  (5u)
//For Clock Setup - END


#define _sign(a) ( ( (a) < 0 )  ?  -1   : ( (a) > 0 ) )
#define _round(x) ((x)>=0?(long)((x)+0.5):(long)((x)-0.5))
#define _constrain(amt,low,high) ((amt)<(low)?(low):((amt)>(high)?(high):(amt)))
#define min(a,b) ((a)<(b)?(a):(b))
#define max(a,b) ((a)>(b)?(a):(b))
#define _sqrt(a) (_sqrtApprox(a))

// utility defines
#define _2_SQRT3 1.15470053838
#define _SQRT3 1.73205080757
#define _1_SQRT3 0.57735026919
#define _SQRT3_2 0.86602540378
#define _SQRT2 1.41421356237
#define _120_D2R 2.09439510239
#define _PI 3.14159265359
#define _PI_2 1.57079632679
#define _PI_3 1.0471975512
#define _2PI 6.28318530718
#define _3PI_2 4.71238898038
#define _PI_6 0.52359877559
#define _2PI_3 2.094395102 //120 deg
#define _4PI_3 4.188790205 //240 deg
#define _SQRT3_2 0.86602540378


#define velocity_limit 20 //[rad/sec]

//This will limit the amount of call to the ADC and observer ?
#define FOC_CONTROL_LOOP_FREQ_DIVIDER	3


//Command for the Magnetic Sensor, can be defined ...
const uint16_t AS5048A_NOP                           = 0x0000; // Dummy operation, no information.
const uint16_t AS5048A_CLEAR_ERROR_FLAG              = 0x0001; // Error register. All errors are cleared by access.
const uint16_t AS5048A_PROGRAMMING_CONTROL           = 0x0003; // Register control programming. Programming must be enabled before the memory is burned. Before programming verification is mandatory. See Programming Procedure.
const uint16_t AS5048A_OTP_REGISTER_ZERO_POS_HIGH    = 0x0016; // Zero value of 8 bits high
const uint16_t AS5048A_OTP_REGISTER_ZERO_POS_LOW     = 0x0017; // Zero value 6 bits lower
const uint16_t AS5048A_DIAG_AGC                      = 0x3FFD; // (0-7) The value of the automatic gain control. 0 decimal represents a high magnetic field, 255 decimal represents a low magnetic field. (8-13) Diagnostics Flags
const uint16_t AS5048A_MAGNITUDE                     = 0x3FFE; // The value of the output power CORDIC
const uint16_t AS5048A_ANGLE                         = 0x3FFF; // Angular output value, including zero position correction Resolution_ADC 14-bit resolution (0.0219 ° / LSB)



static volatile uint32_t microseconds = 0;
unsigned long open_loop_timestamp = 0;
unsigned long velocity_calc_timestamp = 0;
const int sine_array[200] = {0,79,158,237,316,395,473,552,631,710,789,867,946,1024,1103,1181,1260,1338,1416,1494,1572,1650,1728,1806,1883,1961,2038,2115,2192,2269,2346,2423,2499,2575,2652,2728,2804,2879,2955,3030,3105,3180,3255,3329,3404,3478,3552,3625,3699,3772,3845,3918,3990,4063,4135,4206,4278,4349,4420,4491,4561,4631,4701,4770,4840,4909,4977,5046,5113,5181,5249,5316,5382,5449,5515,5580,5646,5711,5775,5839,5903,5967,6030,6093,6155,6217,6279,6340,6401,6461,6521,6581,6640,6699,6758,6815,6873,6930,6987,7043,7099,7154,7209,7264,7318,7371,7424,7477,7529,7581,7632,7683,7733,7783,7832,7881,7930,7977,8025,8072,8118,8164,8209,8254,8298,8342,8385,8428,8470,8512,8553,8594,8634,8673,8712,8751,8789,8826,8863,8899,8935,8970,9005,9039,9072,9105,9138,9169,9201,9231,9261,9291,9320,9348,9376,9403,9429,9455,9481,9506,9530,9554,9577,9599,9621,9642,9663,9683,9702,9721,9739,9757,9774,9790,9806,9821,9836,9850,9863,9876,9888,9899,9910,9920,9930,9939,9947,9955,9962,9969,9975,9980,9985,9989,9992,9995,9997,9999,10000,10000};


static volatile uint32_t _ulTickCount=0 ;



static volatile float angle_prev =0;

static int angle_data_prev = 0;
float full_rotation_offset = 0.0; //!<number of full rotations made


unsigned long previousMillis =0;
long interval = 1000;

volatile uint32_t pwm_min = 10000;
volatile uint32_t pwm_max = 0;


uint8_t rx_data_buffer[20]; // buffer for data reception
uint8_t tmp_buffer[20]; // temporary buffer



_Bool error_flag = 0;


float FOC_target = 0;


float shaft_angle_sp =0;
float shaft_velocity_sp = 0;

static _Bool aprox_trig = FALSE;

// 1 -> Clock Wise
// -1 -> Counter Clock Wise
int sensor_direction = NONE;


// What ?
float zero_electric_angle = 0;


// BEGIN - Current Sensing Variables
_Bool current_sense = DISABLED;
// END - Current Sensing Variables

//The type of motion the motor will perform
int motion_control_type = ANGLE_OPENLOOP;



//Objects for PID Control
PID_struct PID_velocity_obj;
PID_struct PID_angle_obj;
PID_struct PID_Iq_obj;
PID_struct PID_Id_obj;

//Objects for Low Pass Filter
LPF_struct LPF_velocity_obj;
LPF_struct LPF_angle_obj;
LPF_struct LPF_Iq_obj;
LPF_struct LPF_Id_obj;

//Motor Object
MOTOR_struct MOTOR_obj;

//Current Sense Object
CURRENT_SENSE_struct CURRENT_obj;

//PWM Object
PWM_struct PWM_obj;

//Observer Object
OBSERVER_struct OBSERVER_obj;


float buffer[64];
uint8_t buffer_pos=0;
uint8_t buffer_pos_1=0;

int enabale_ob = FALSE;

void observer();
void set_up_PWM_obj();
void set_up_motor_obj();
void set_up_current_obj();
void get_currents(float electrical_angle);
void FOC(float target);
float shaftVelocity(float _current_angle);
float shaftAngle();
void modulate(float Uq, float Ud, float angle_el);
void angular_sensor_calibrate();
float getAngle();
void set_up_LPF();
void set_up_PID();
float LPF(float value, struct LPF_struct *LPF_obj);
float PID(float err, struct PID_struct *PID_obj);
float _sqrtApprox(float number);
unsigned long millis( void );
void delay( unsigned long ms );
float getVelocity(float _current_angle);
void velocity_OL(float target_velocity);
float electricalAngle(float _angle);
void velocity_CL(float target_velocity);
void Angle_CL(float target_angle);
void Angle_OL(float target_velocity);
void SinePWM(float Uq, float Ud, float angle_el);
void SpaceVectorPWM(float Uq, float Ud, float angle_el);
void delayMicroseconds(unsigned int us);
unsigned long micros( void );
void setPhaseVoltage(float Uphase_1, float Uphase_2, float Uphase_3);
float _cos(float a);
float _sin(float a);
float _normalizeAngle(float angle);
float _electricalAngle(float shaft_angle, int pole_pairs) ;
void TC0_Handler();
void TCC0_0_Handler();
void TCC0_setup();
void set_TC0();
void PINs_setup();
uint16_t AS5048A_send_command(int cmd);
uint16_t AS5048A_read_angle();
char CalcEvenParity(uint16_t Value);
uint8_t  SPI_transfer_8_bits(uint8_t data);
uint16_t SPI_transfer_16_bits(uint16_t data);
void set_up_SPI_SERCOM_5(uint32_t baudrate);
void set_up_clocks();
void voltage_ref_setup();
void set_up_ADC0();
uint32_t ADC_Read(int phase);
void usb_data_received(uint8_t status, uint16_t length) ;
void set_usb_config(uint8_t index) ;
void set_up_systick() ;
void SysTick_Handler();
void dwt_enable(void);

void observer(){
	
	OBSERVER_obj.timestamp_now = micros();
	
	float xa_d, xb_d;
	float err;
	float theta;
	
	const float L = (3.0 / 2.0) *MOTOR_obj.inductance;
	float R = (3.0 / 2.0) *MOTOR_obj.phase_resistance;
	
	/*
	const float L = MOTOR_obj.inductance;
	float R = MOTOR_obj.phase_resistance;
	*/
	//Inductive Components
	const float LI_A = MOTOR_obj.I_alpha*L;
	const float LI_B = MOTOR_obj.I_beta*L; 
	//Resistive Components
	const float RI_A = MOTOR_obj.I_alpha*R;
	const float RI_B = MOTOR_obj.I_beta*R;
	const float FL_2 = pow(MOTOR_obj.flux_linkage,2);

	const float gain_half = MOTOR_obj.observer_gain;;

	
	
	
	err = FL_2 - (pow((OBSERVER_obj.xa-LI_A),2)+pow((OBSERVER_obj.xb-LI_B),2));
	
	xa_d = -RI_A + MOTOR_obj.U_alpha + gain_half*(OBSERVER_obj.xa- LI_A)*err;
	xb_d = -RI_B + MOTOR_obj.U_beta + gain_half*(OBSERVER_obj.xb- LI_B)*err;

	float dt = (OBSERVER_obj.timestamp_now - OBSERVER_obj.timestamp_prev)*1e-6;



	OBSERVER_obj.xa += (xa_d * dt);
	OBSERVER_obj.xb += (xb_d * dt);
	

	
	UTILS_NAN_ZERO(OBSERVER_obj.xa);
	UTILS_NAN_ZERO(OBSERVER_obj.xb);
	
	theta = atan2(OBSERVER_obj.xb - LI_B, OBSERVER_obj.xa - LI_A);
	
	OBSERVER_obj.timestamp_prev = OBSERVER_obj.timestamp_now;
	
	MOTOR_obj.estimated_angle = theta+3;
	
	buffer[buffer_pos++]= MOTOR_obj.estimated_angle;
	buffer[buffer_pos+15] = MOTOR_obj.electrical_angle;
	buffer[buffer_pos+31]= OBSERVER_obj.xa;
	buffer[buffer_pos+47]= OBSERVER_obj.xb;
	if (buffer_pos==(sizeof(buffer)/sizeof(buffer[0]))/4){
		buffer_pos=0;
		usb_send_bulk_data((uint8_t*)buffer,sizeof(buffer),NULL);
	}
	

}

void set_up_observer_obj(){
	
	
	//Setting the Flux Linkage
	//OBSERVER_obj.flux_linkage = 0.0024; //[Wb]
	
	OBSERVER_obj.flux_linkage = 0.004; //[Wb]
	
	//Setting the observers gain
	OBSERVER_obj.observer_gain = 4000;
	
	OBSERVER_obj.xa = 0;
	OBSERVER_obj.xb = 0;
	
	OBSERVER_obj.timestamp_prev= micros();
	OBSERVER_obj.timestamp_now = micros();
	
	
}

void set_up_PWM_obj(){

	//Set up the PWM Resolution
	PWM_obj.PWM_resolution = 1000;

	//Setup the Type of Modulation -> Sineusoid Modulation by default
	PWM_obj.modulation_type = SINE_PWM;

	//Set the power supply voltage
	PWM_obj.voltage_power_supply = 12.0;

	//Set the voltage limit to the motor
	PWM_obj.voltage_limit = 2.0;
}

void set_up_motor_obj(){

	//Is the motors angle estimated by current ?
	MOTOR_obj.sensorless = FALSE;

	//Motor State Enable
	MOTOR_obj.motor_state = ENABLED;

	//We Set the phase resistance of the motor
	MOTOR_obj.phase_resistance = 1.6; //[Ohms]

	//Set up the number of pole pairs
	MOTOR_obj.pole_pairs = 7;

	//Set inductance	//We need to measure it...
	MOTOR_obj.inductance = 0.00002;
	
	

	//Setting the Current Limit
	MOTOR_obj.current_limit = 1.0; // [Amps]
	

	


}

void set_up_current_obj(){

	//Shunt Resitor Value ... 3mOhm
	CURRENT_obj.shunt_resistor = 0.003;

	//Bit rate
	//For 10 bits
	CURRENT_obj.bit_rate = pow(2,10);
	//For 12 bits
	//CURRENT_obj.bit_rate = pow(2,12);

	//gain of OP Amps
	//gain of the Amps are set to 20
	CURRENT_obj.gain = 20;

	//Reference Voltage of ADC
	//Refence Voltage is set to 3.3V
	CURRENT_obj.reference_voltage = 3.3;
	//CURRENT_obj.reference_voltage = 1.0;

	//Calculate Conversion
	//Using the following eqaution = V_measure = ADC_value*(ADC_V_ref/ADC_bit_rate)
	CURRENT_obj.conversion_scalar = CURRENT_obj.reference_voltage/CURRENT_obj.bit_rate;

	//Set offsets to Zero until they are calculated
	CURRENT_obj.I_phase_A_offset = 0;
	CURRENT_obj.I_phase_B_offset = 0;
 	CURRENT_obj.I_phase_C_offset = 0;
	
	//Calculating Volt to Amp Ratio --> Multiplying the Voltage by this will give us the current
	CURRENT_obj.volts_to_amps_ratio = 1.0 /CURRENT_obj.shunt_resistor / CURRENT_obj.gain; 

	//Saving the V/I ratio for each phase.
	CURRENT_obj.I_gain_phase_A = CURRENT_obj.volts_to_amps_ratio;
	CURRENT_obj.I_gain_phase_B = CURRENT_obj.volts_to_amps_ratio;
	CURRENT_obj.I_gain_phase_C = CURRENT_obj.volts_to_amps_ratio;

	const int calibration_rounds = 1000;

	//Here we will calculate the average offset off phase	
	
	for (int i = 0; i < calibration_rounds; i++) {
		volatile uint32_t p_a = ADC_Read(PHASE_A);
		CURRENT_obj.I_phase_A_offset += p_a*CURRENT_obj.conversion_scalar;
		CURRENT_obj.I_phase_B_offset += ADC_Read(PHASE_B)*CURRENT_obj.conversion_scalar;
		CURRENT_obj.I_phase_C_offset += ADC_Read(PHASE_C)*CURRENT_obj.conversion_scalar;
		delay(1);
	}

	//We calculate the mean offsets 
	CURRENT_obj.I_phase_A_offset = CURRENT_obj.I_phase_A_offset / calibration_rounds;
	CURRENT_obj.I_phase_B_offset = CURRENT_obj.I_phase_B_offset / calibration_rounds;
	CURRENT_obj.I_phase_C_offset = CURRENT_obj.I_phase_C_offset / calibration_rounds;

	//Offset should now be calibrated.
}

void get_FOC_currents(float electrical_angle){
	
	/*
	CURRENT_obj.read_currents = TRUE;
	
	//Wait for currents to be read by TCC0 interupt
	while(CURRENT_obj.read_currents);

	//Currents have been read, we now convert them from RAW form to Voltage form
	CURRENT_obj.I_raw_phase_A_voltage = CURRENT_obj.I_raw_phase_A*CURRENT_obj.conversion_scalar;
	CURRENT_obj.I_raw_phase_B_voltage = CURRENT_obj.I_raw_phase_B*CURRENT_obj.conversion_scalar;
	CURRENT_obj.I_raw_phase_C_voltage = CURRENT_obj.I_raw_phase_C*CURRENT_obj.conversion_scalar;
	
	//CURRENT_obj.I_raw_phase_C_voltage = CURRENT_obj.I_raw_phase_A_voltage + CURRENT_obj.I_raw_phase_B_voltage;

	//We now subtract the offset of the current sensing and apply the Voltage to Current conversion
	MOTOR_obj.I_phase_A = (CURRENT_obj.I_raw_phase_A_voltage - CURRENT_obj.I_phase_A_offset)*CURRENT_obj.I_gain_phase_A;// amps
	MOTOR_obj.I_phase_B = (CURRENT_obj.I_raw_phase_B_voltage - CURRENT_obj.I_phase_B_offset)*CURRENT_obj.I_gain_phase_B;// amps
	MOTOR_obj.I_phase_C = (CURRENT_obj.I_raw_phase_C_voltage - CURRENT_obj.I_phase_C_offset)*CURRENT_obj.I_gain_phase_C;// amps

	//We Calculate the current in Phase C using KCL
    //MOTOR_obj.I_phase_C = MOTOR_obj.I_phase_A + MOTOR_obj.I_phase_B ;

	/*

	// signal filtering using identity a + b + c = 0. Assumes measurement error is normally distributed.	
	float mid = (1.f/3) * (MOTOR_obj.I_phase_A + MOTOR_obj.I_phase_B  + MOTOR_obj.I_phase_C );
	float a = MOTOR_obj.I_phase_A - mid;
	float b = MOTOR_obj.I_phase_B - mid;
	//Calculate Clarke Transform
	MOTOR_obj.I_alpha = a;
	MOTOR_obj.I_beta = _1_SQRT3 * a + _2_SQRT3 * b;
	*/
	
	/*
	MOTOR_obj.I_alpha = (2.f/3)*MOTOR_obj.I_phase_A - (1.f/3)*(MOTOR_obj.I_phase_B-MOTOR_obj.I_phase_C);
	MOTOR_obj.I_beta = _2_SQRT3*(MOTOR_obj.I_phase_B - MOTOR_obj.I_phase_C);
	*/
	
	MOTOR_obj.I_alpha = MOTOR_obj.I_phase_A;
	MOTOR_obj.I_beta = _1_SQRT3*MOTOR_obj.I_phase_A + _2_SQRT3*MOTOR_obj.I_phase_B;
	
	/*
	buffer[buffer_pos++]=MOTOR_obj.I_alpha;
	if (buffer_pos==sizeof(buffer)/sizeof(buffer[0])){
		buffer_pos=0;
		usb_send_bulk_data((uint8_t*)buffer,sizeof(buffer),NULL);
	}
	*/

	float ct;
	float st;
	
	if(aprox_trig){
		ct = _cos(electrical_angle);
		st = _sin(electrical_angle);
	}else{
		ct = cos(electrical_angle);
		st = sin(electrical_angle);
	}
	//Calculate Park Transform	
	MOTOR_obj.I_d = MOTOR_obj.I_alpha * ct + MOTOR_obj.I_beta * st;
	MOTOR_obj.I_q = MOTOR_obj.I_beta * ct - MOTOR_obj.I_alpha * st;
	
	
	MOTOR_obj.I_d = LPF(MOTOR_obj.I_d,&LPF_Id_obj);
	MOTOR_obj.I_q = LPF(MOTOR_obj.I_q,&LPF_Iq_obj);
	
}


 int skip_count = 10;

void FOC(float target){
	
	
	//If the motor is disabled we do nothing
	if(MOTOR_obj.motor_state == DISABLED){
		setPhaseVoltage(0,0,0);
		return;
	}
	
	skip_count++;
	
	if(enabale_ob == TRUE){
		observer();	
	}
	
	
	if(skip_count >10){
		skip_count=0;
		
	}



	

	
	/*	
	
	buffer[buffer_pos++]=  MOTOR_obj.estimated_angle;
	buffer[buffer_pos+31] = 0;
	if (buffer_pos==(sizeof(buffer)/sizeof(buffer[0]))/2){
		buffer_pos=0;
		usb_send_bulk_data((uint8_t*)buffer,sizeof(buffer),NULL);
	}
	
	

	*/
	
	switch (motion_control_type){
		
		case VELOCITY_OPENLOOP:
			velocity_OL(target);
			MOTOR_obj.shaft_velocity = target;	
			//get_FOC_currents(MOTOR_obj.electrical_angle);
			return;
			break;
			
		case ANGLE_OPENLOOP:
			Angle_OL(target);
			MOTOR_obj.shaft_angle = target;
			//get_FOC_currents(MOTOR_obj.electrical_angle);
			return;
			break;
		
		case VELOCITY:
			velocity_CL(target);
			
			break;
		
		case ANGLE:
			Angle_CL(target);
			//get_FOC_currents(MOTOR_obj.electrical_angle);
			break;

			
	}
	
	
	
	
	get_FOC_currents(MOTOR_obj.electrical_angle);

	
	if(current_sense == ENABLED){
		
		/*
		MOTOR_obj.I_q = LPF(MOTOR_obj.I_q, &LPF_Iq_obj);
		MOTOR_obj.I_d = LPF(MOTOR_obj.I_d, &LPF_Id_obj);
		*/	
		MOTOR_obj.U_q = PID(MOTOR_obj.current_sp - MOTOR_obj.I_q, &PID_Iq_obj);
		MOTOR_obj.U_d = PID(-MOTOR_obj.I_d, &PID_Id_obj);
		
	}
	
	
	modulate(MOTOR_obj.U_q, MOTOR_obj.U_d, MOTOR_obj.electrical_angle);

}

float shaftVelocity(float _current_angle) {
	// if no sensor linked return previous value ( for open loop )
	
	return sensor_direction*LPF(getVelocity(_current_angle),&LPF_velocity_obj);
}

float shaftAngle(){
	
	return sensor_direction*LPF(getAngle(), &LPF_angle_obj);
}

void modulate(float Uq, float Ud, float angle_el){
	
	switch(PWM_obj.modulation_type){
		case SINE_PWM:
			SinePWM(Uq, Ud, angle_el);
			break;
		case SPVM:
			SpaceVectorPWM(Uq, Ud, angle_el);
			break;	
	}
	
}
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
int main(void)
{
	memset(buffer,sizeof(buffer[0])*64,0);
	
	open_loop_timestamp = micros();
	velocity_calc_timestamp = micros();
	PINs_setup();
	voltage_ref_setup();
	set_up_PWM_obj();
	set_up_motor_obj();
	set_up_clocks();
	set_up_systick();
	usb_register_set_config_callback(set_usb_config);
	usb_init(GENERIC_CLOCK_GENERATOR_48M);
	//set_TC0();
	set_up_ADC0();
	set_up_current_obj();
	TCC0_setup();
	set_up_SPI_SERCOM_5(10000000); //10MHz
	dwt_enable();
	set_up_LPF();
	set_up_PID();
	//Incase there are any errors in the magnetic sensor
	AS5048A_send_command(AS5048A_CLEAR_ERROR_FLAG);
	setPhaseVoltage(0,0,0);
	delay(1);
	unsigned long current = millis();
	unsigned long previous = millis();
	
	while(sensor_direction == NONE){
		angular_sensor_calibrate();
	}

	RESET(LED4)
	RESET(LED5)
	MOTOR_obj.motor_state = ENABLED;
	motion_control_type = VELOCITY;
	//motion_control_type = VELOCITY_OPENLOOP;
	//motion_control_type = ANGLE;
	//motion_control_type = ANGLE_OPENLOOP;
	
	//rad/sec for Velocity Control
	//rad for Angle Control
	FOC_target = 20;
		
		
	current_sense = DISABLED;

	aprox_trig = FALSE;
	PWM_obj.modulation_type = SINE_PWM;

	while(1){

		FOC(FOC_target);
		


			
		current = millis();
		if (current - previous >= 1000) {
			previous = millis();
			
			enabale_ob = TRUE;
			/*
			if(FOC_target == 100){
				FOC_target = -100;	
			}else{
				FOC_target = 100;		
			}*/
				
		}
		
			
	}
	
	
}

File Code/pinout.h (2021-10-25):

#ifndef PINOUT_H_
#define PINOUT_H_

//SPI
#define MISO			PB,01 //SERCOM-5 PAD[3]
#define CLK				PB,03 //SERCOM-5 PAD[1]
#define MOSI			PB,02 //SERCOM-5 PAD[0]
#define CS				PB,00 //SERCOM-5 PAD[2]

#define EX_1			PA,04 //SERCOM-0 PAD[0]
#define EX_2			PA,05 //SERCOM-0 PAD[1]
#define EX_3			PA,06 //SERCOM-0 PAD[2]
#define EX_4			PA,07 //SERCOM-0 PAD[3]
//LEDs
#define LED1			PA,00
#define LED2			PA,01
#define LED4			PB,23
#define LED5			PB,22

//Buttons
#define BTN1			PB,11
#define BTN2			PB,10

//Phase Control
#define P1_HS_LOGIC		PA,22
#define P2_HS_LOGIC		PA,21
#define P3_HS_LOGIC		PA,20

#define P1_LS_LOGIC		PA,18
#define P2_LS_LOGIC		PA,17
#define P3_LS_LOGIC		PA,16

//Phase Current Sense
#define I_PHASE_1		PA,10
#define I_PHASE_2		PA,9
#define I_PHASE_3		PA,8

//USB
#define USBP			PA,25
#define USBM			PA,24


#endif /* PINOUT_H_ */

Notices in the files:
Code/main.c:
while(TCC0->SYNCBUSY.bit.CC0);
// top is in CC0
